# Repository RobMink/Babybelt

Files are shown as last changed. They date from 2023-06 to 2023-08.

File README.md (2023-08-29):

# Babybelt
Hello!  Welcome to the github repo for Babybelt!

****
BabyBelt Pro is at https://github.com/RobMink/BabyBeltPro
****

Extruder, rolleridler Right side and tentionarm need support

www.printcepts.com

BOM:https://docs.google.com/spreadsheets/d/1HSS2FmvWl4BJgFne0Ccxiv6K9c1OWvDrwnjKOO4NND4/edit?usp=sharing

per version changes: https://docs.google.com/spreadsheets/d/1RWIczKBFYHM32IPGfSvWw3lULVfq1J2buDYnhtqqLhI/edit?usp=sharing

DISCORD:   https://discord.gg/nVmeNJJSH2BB   - Note, remove BB at the end of the link.  Done to eleminate spam bots.

Youtube: www.youtube.com/c/robmink

Facebook https://www.facebook.com/groups/632751915097010

If you wish to support the project : https://www.patreon.com/Printcepts

•	45 Degree belt printer 90 mm by 86 mm ish axis

•	Sensorless Homing

•	28BJY48 motors

•	Mostly 3d printed

•	Belt is iron on cloth on fabric

•	Runs on Marlin

**Design philosophy and considerations in order of importance:**

Cheap. Target price if put into mass production around $100. During development and bootstrapping periods $200. 

Cheap. I know we said that already but it's important.

Simple and easy to assemble

Reuse of common parts and limiting of fasteners

Assembled printer must fit in the priority mail prepaid box. 

**What makes the baby belt special**

Use of smallest cheapest stepper motors ever

Use of 3mm round rods with 3mm PtfE tubes used as bearings

Simple iron on belt made from fabric and iron on material along with use of jigs for repeatability. 

Smallest belt printer ever (as of right now)

Cantilever arm

Easily broken down for storage or transport and easy setup with two clip together assemblies for the whole machine.

Sensorless homing.

Aerodynamic exit ramp for parts.

Only two types of screws used for every thing (discipline design approach reducing overall BOM cost)

Non commerical,  Help from Autodrop3d's mmiscool, Ottersdangerden and NAK-3d.

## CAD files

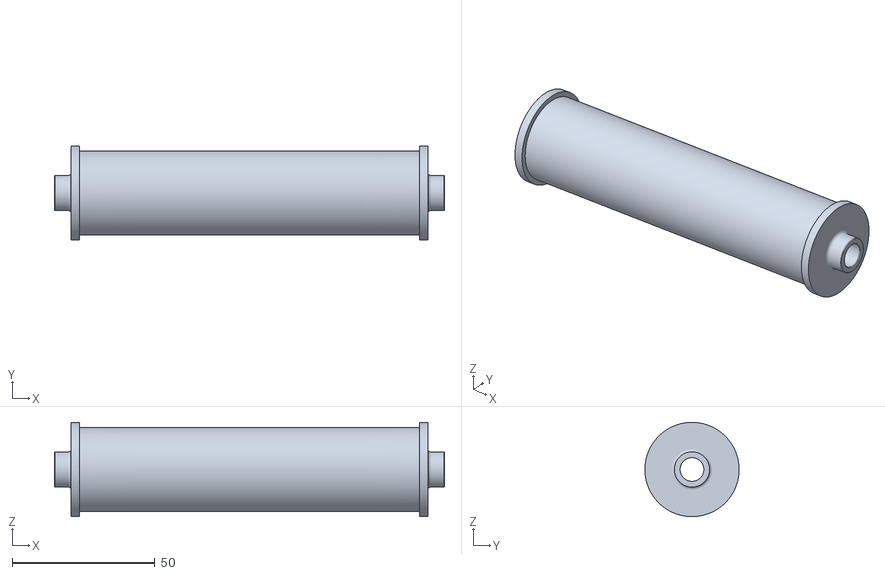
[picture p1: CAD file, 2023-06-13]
bb11-0_printedfullroller_5.stl
136.6 x 33.0 x 33.0

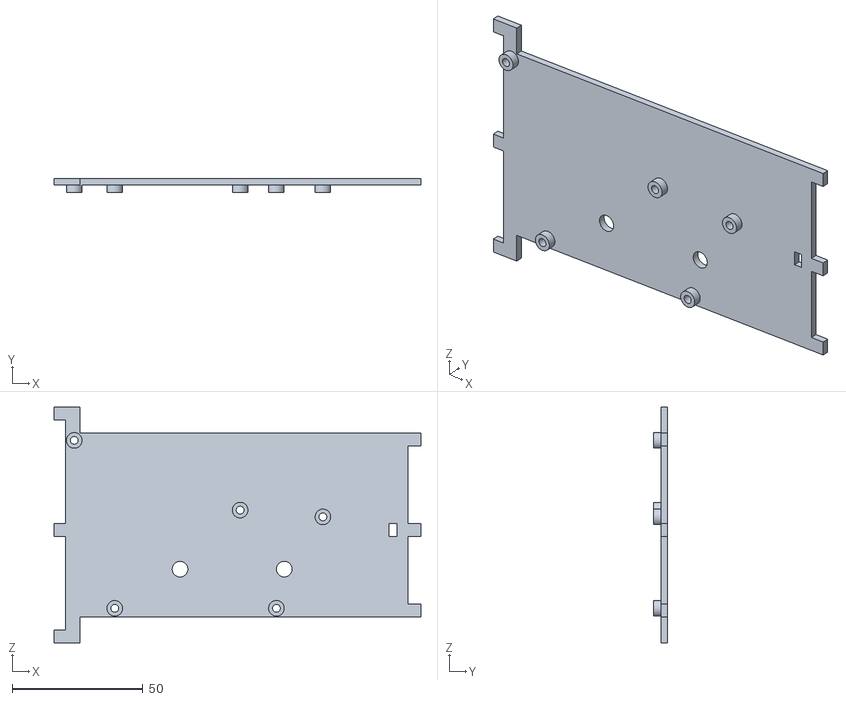
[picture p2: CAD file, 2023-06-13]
bb11-0_mksgenholderfull_41.stl
140.5 x 5.50 x 90.3

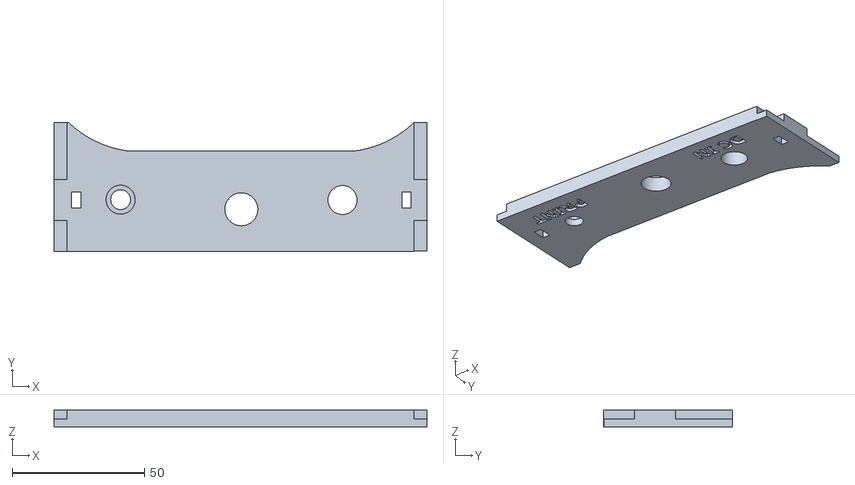
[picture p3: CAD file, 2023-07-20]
Front Cross Brace.stl
141.1 x 48.7 x 6.42

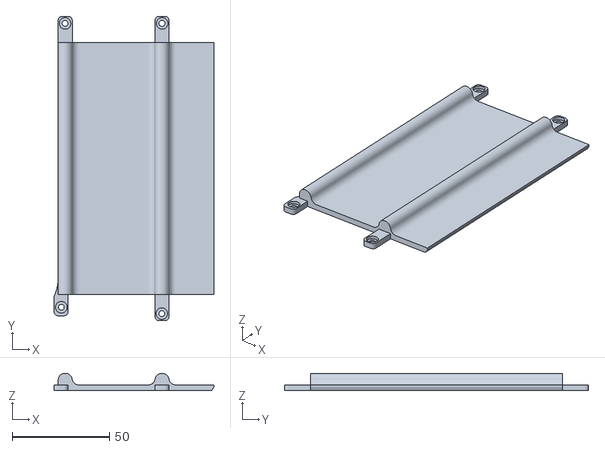
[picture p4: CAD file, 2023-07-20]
UnderbedSupport.stl
82.4 x 156.8 x 9.00

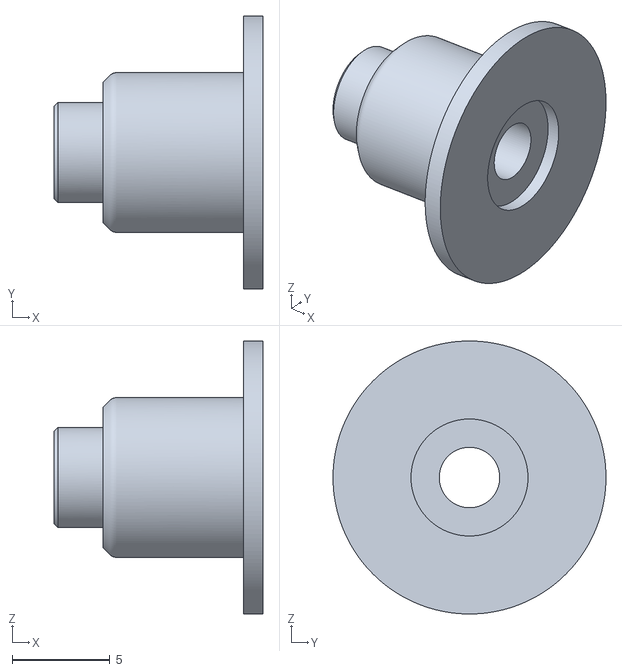
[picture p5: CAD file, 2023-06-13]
bb11-0_extruderhelperpin_48.stl
10.7 x 14.0 x 14.0

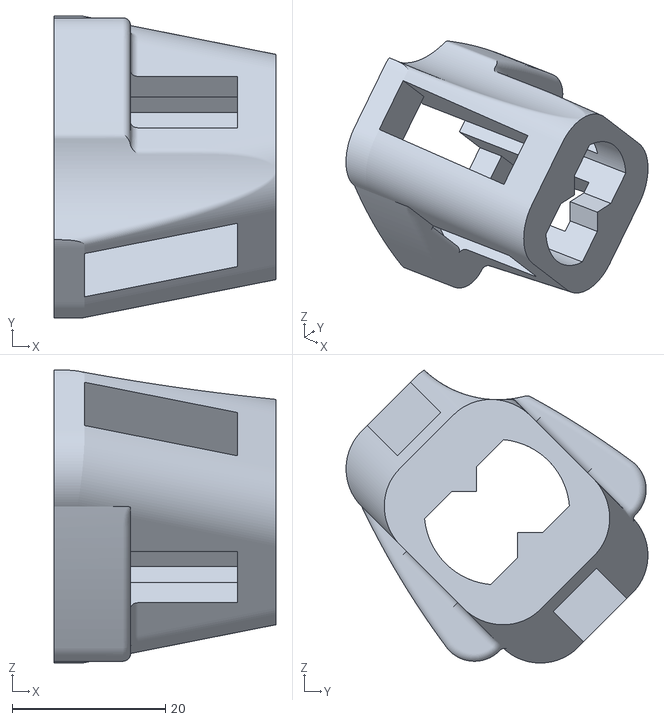
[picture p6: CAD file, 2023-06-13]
bb11-0_XTentioner_29.stl
29.0 x 39.4 x 38.3

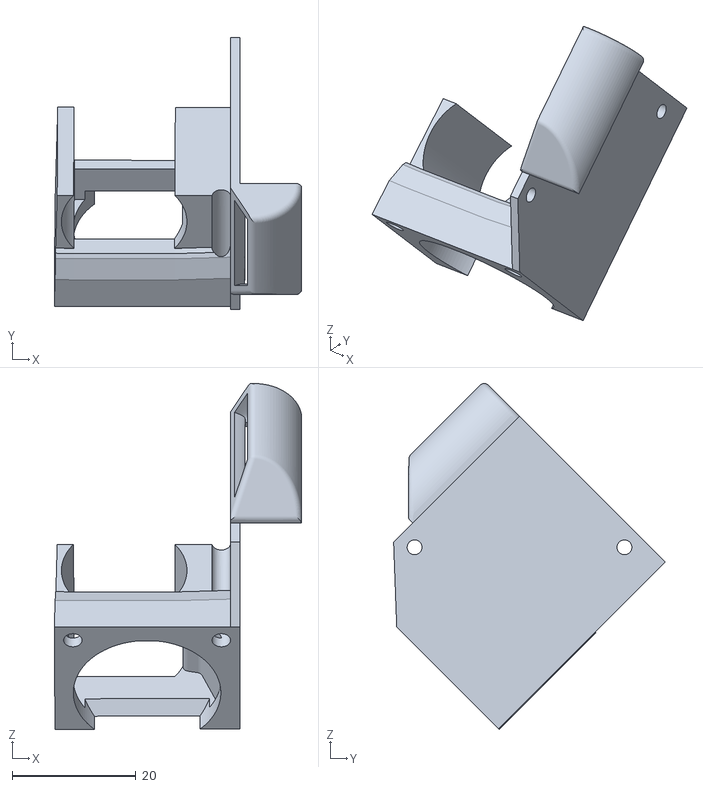
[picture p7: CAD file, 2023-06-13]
bb11-0_fanduct.0006_25.stl
40.0 x 44.0 x 56.0

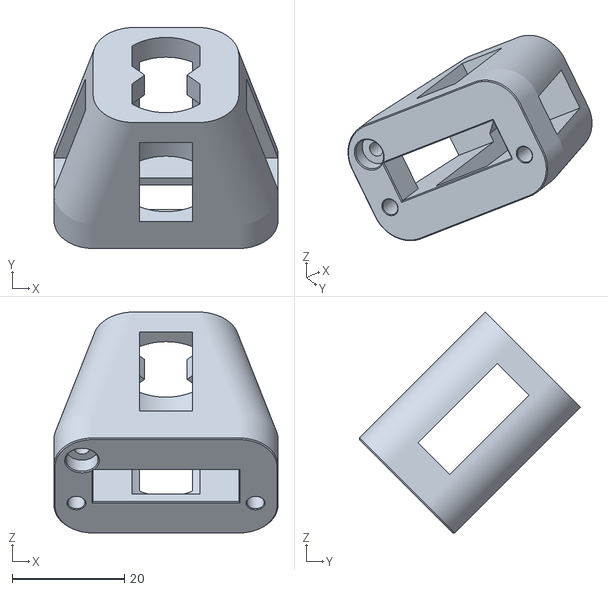
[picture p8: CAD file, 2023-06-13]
bb11-0_RockMonsterNo1YTentionerPart6_28.stl
40.0 x 39.5 x 39.5

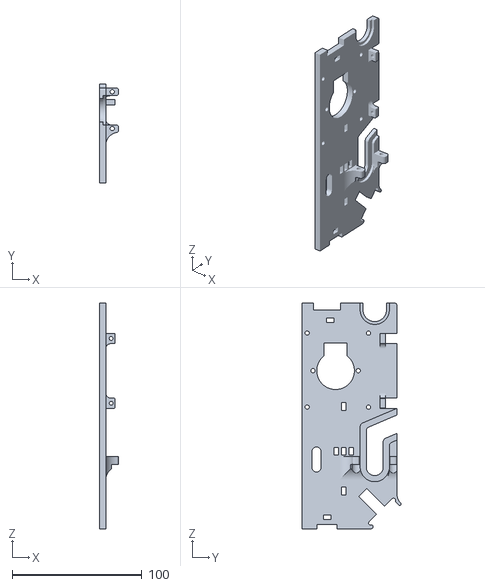
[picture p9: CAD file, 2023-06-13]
bb11-0_leftsideforgears_2.stl
15.0 x 76.5 x 174.3

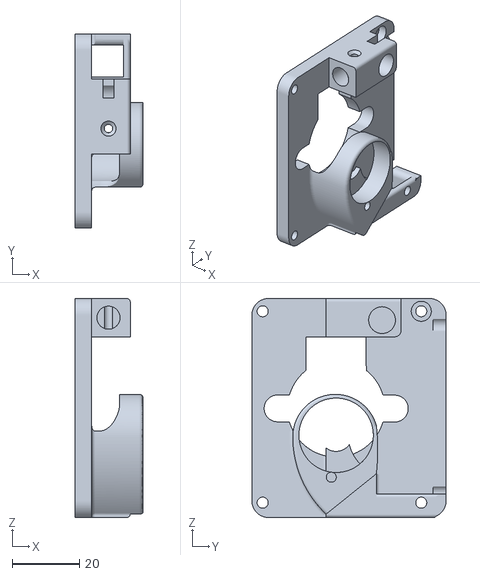
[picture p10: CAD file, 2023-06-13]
bb11-0_ModularExtruderMK8_42.stl
20.3 x 58.0 x 65.4

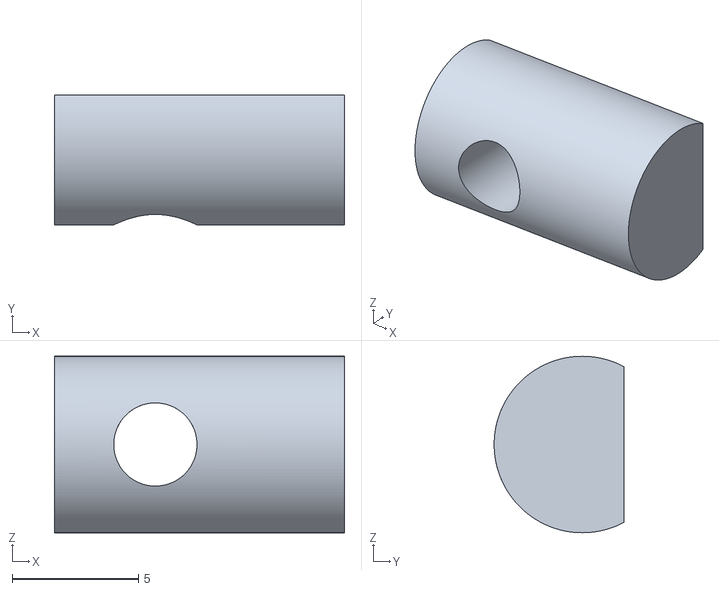
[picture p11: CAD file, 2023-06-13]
bb11-0_TentionArmClip_50.stl
11.5 x 5.15 x 7.00

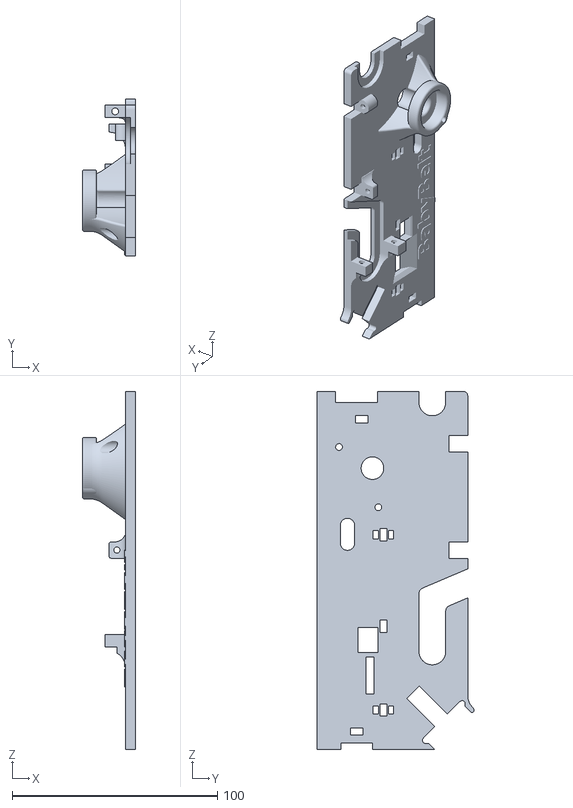
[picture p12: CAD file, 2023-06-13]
bb11-0_rightsideforwormgears (2)_4.stl
26.0 x 76.5 x 174.3

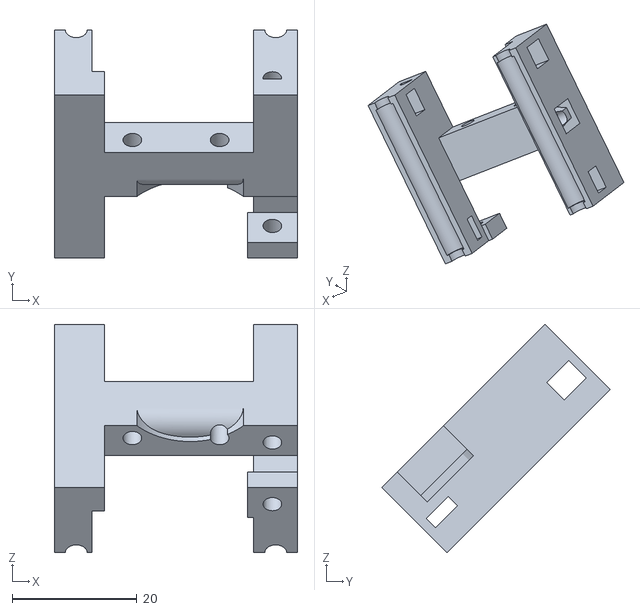
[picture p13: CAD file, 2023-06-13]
bb11-0_Yslider-Updated_18.stl
39.0 x 36.6 x 36.6

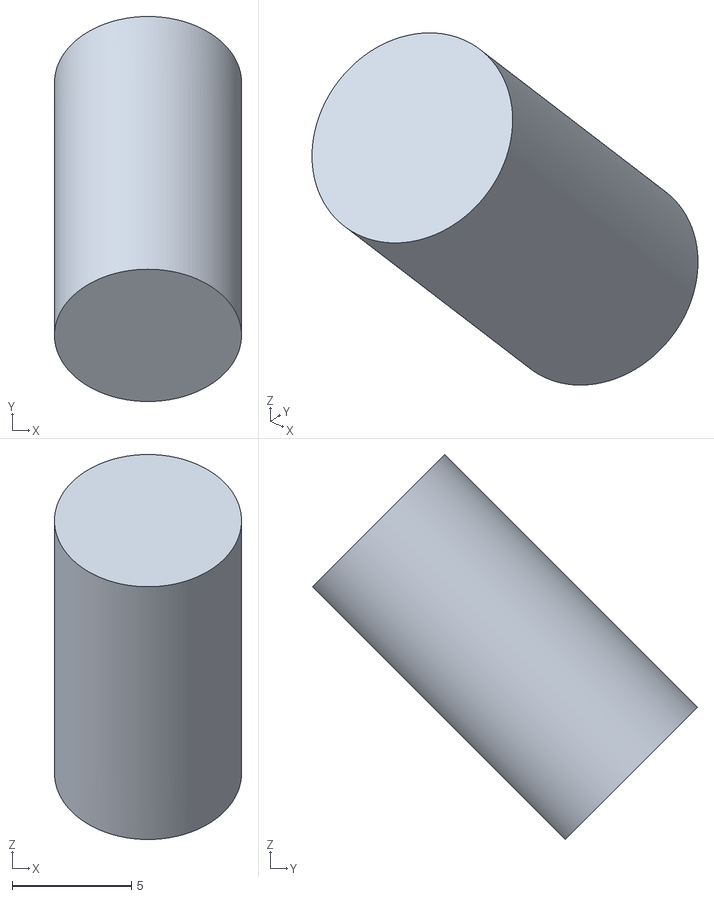
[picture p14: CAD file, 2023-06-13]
bb11-0_608endstopaxle_24.stl
7.85 x 16.2 x 16.2

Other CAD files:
bb11-0_printedfullroller_10.stl
bb11-0_XTentionerNut_30.stl
bb11-0_xbeltholderleftandmotortoo-28byj48-2_17.stl
bb11-0_Spur Gear11_55.stl
bb11-0_608endstopaxle_33.stl
bb11-0_BB38PullybaseScad38toothgear001 (Solid)001_36.stl
bb11-0_BB38PullybaseScad38toothgear001 (Solid)001_37.stl
bb11-0_Beltlocker_51.stl
bb11-0_ExtruderTentonArmPin_49.stl
bb11-0_Peeler_3.stl
bb11-0_RockMonsterNo1YTentionerNut_27.stl
bb11-0_RockMonsterNo1YTentionerScrew_26.stl
bb11-0_Spur Gear21_56.stl
bb11-0_XTentionerScrew_31.stl
bb11-0_beltpuller_53.stl
bb11-0_beltpuller_MIR_54.stl
bb11-0_newXslider 28byj48-updated_19.stl
bb11-0_tentonarm_43.stl
bb9-4.stp
jig.stl

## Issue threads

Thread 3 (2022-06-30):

Gear cover does NOT fit

RobMink, 2022-06-30:
I am aware that the gear cover does not fit the current build.  Low priority, but it will get fixed.  Thanks!

RobMink, 2023-06-13:
overcome by events, that was a V9 build issue.

Closed 2023-06-13.

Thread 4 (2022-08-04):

Jig is very large

jakobtolstrup, 2022-08-04:
The jig.stl file results in a Ø196mm or 616mm long belt. Shouldn't the diameter be around 91mm

RobMink, 2022-08-05:
Yep, you are 100% correct, it was way too large.  Fixed now, sorry about that!  It is 98.61 MM diameter and 125 MM tall.

RobMink, 2022-08-05:
Updated file, commented!

jakobtolstrup, 2022-08-05:
Awesome, thanks

Closed 2022-08-05.

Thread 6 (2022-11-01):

Need a link for a full STL/OBJ package

inspectionsbybob, 2022-11-01:
Looking at the files, I was hoping there was a link somewhere to download  -ALL- the STLs or OBJ files at once...

drdelaney, 2022-11-01:
From the main page, click on the down arrow on the green "Code" button. Click "Download ZIP."
This will download the entire branch of what branch you have selected (by default, it is main, but it looks like there are others).

RobMink, 2023-06-13:
As noted by @drdelaney, also full step file has been in there for a while....

Closed 2023-06-13.

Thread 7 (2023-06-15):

Print button does not fit into front support as it is now too thick.

RobMink, 2023-06-15:

RobMink, 2023-07-20:
Fixed!  Added relief.

Closed 2023-07-20.

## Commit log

2022-03-10 Add files via upload
    Y slider updated for more travel, notch cut out in extruder side for fan for extra travel, extruder side cleaned for modular extruder options. NAK-3d desgined BMG geared extruder, NAK-3d suggested du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
2022-03-10 Add files via upload
    Jig for making belt, print in vase mode no top. To make the belt, cut a sheet of construction paper in half length wise. Wrap around Jig. Apply 3 bands of carpet tape, add fabric belt top onto carpet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
    [jig.stl]
2022-03-12 Add files via upload
    Updated Extruder with mk8 gear and 608 bearing. Fixed notch location so it clears the fan in the Y stepper.
2022-03-30 Add files via upload
    updated extruder setup.
2022-04-03 Add files via upload
    Printable files from 9-3. Note that you will need to orient the files correctly on the bed.
2022-04-18 Add files via upload
    Minor tweaks to hole sizes for y end stop, X slider, and extruder body.
    [bb9-4.stp]
2022-04-18 Add files via upload
    full upload, changes are y end stop, extruder, and x slider. Just changes to hole sizes.
2022-05-28 Trimmed worm gear gear if the drive belt binds.
    [Worm Gear-trimmed.stl]
2022-06-13 Add files via upload
    9-5! Made the trimmed worm gear standard, and new Y slider with moved fan for better cooling.
2022-07-16 Add files via upload
    Beta 9.6 - major changes to rollers and fan ducts, ease of assembly changes to x slider, light changes to y slider
2022-08-05 Add files via upload
    updated jig, sorry about that.
    [jig.stl]
2022-09-20 Init Release of BB10-0-1 Beta. Will next release will be 10.1
    Use 120MM Pipe, update the firmware, print and have fun!
2022-10-12 Upload 10.0.2 Not tested yet.
    New 10.0.2 Fixes issues in 10.0.1 beta. Resolves issues with X gantry bring too wide, extruder 608 working loose, enlarging hole on extruder size to clear roller nut, and converted rollers to be printable.
    [bb10-0-2_608XPulleyBlock.stl, bb10-0-2_608YEndStop.0004.stl, bb10-0-2_608endstopaxle.stl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]
2022-10-12 Firmware. Fixes some homing issue and steps
    Fixes homing issues and steps per MM for V10.
2022-10-15 10.1 Update
    tested 10.1
    [bb10-1_printedroller.stl, bb10-1_printedrolleridler.stl, bb10_1_608XPulleyBlock.stl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]
2022-10-27 10,1.1 update
    Minor tweaks to files for printability. Also, parts have been positioned for better printing layout.
    [608XPulleyBlock.stl, 608YEndStop.0004.stl, 608endstopaxle.stl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]
2023-06-13 Add files via upload
    first release of 11, may have minor issues
    [bb11-0_608endstopaxle_24.stl, bb11-0_608endstopaxle_33.stl, bb11-0_BB38PullybaseScad38toothgear001 (Solid)001_36.stl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]
2023-07-20 New Underbed. Stronger and less likely to warp
    [UnderbedSupport.stl]
2023-07-20 New front cross brace, has relief for print button
    [Front Cross Brace.stl]
